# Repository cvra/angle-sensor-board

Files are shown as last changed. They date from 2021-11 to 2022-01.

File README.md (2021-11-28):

# Carte Codeur Absolu

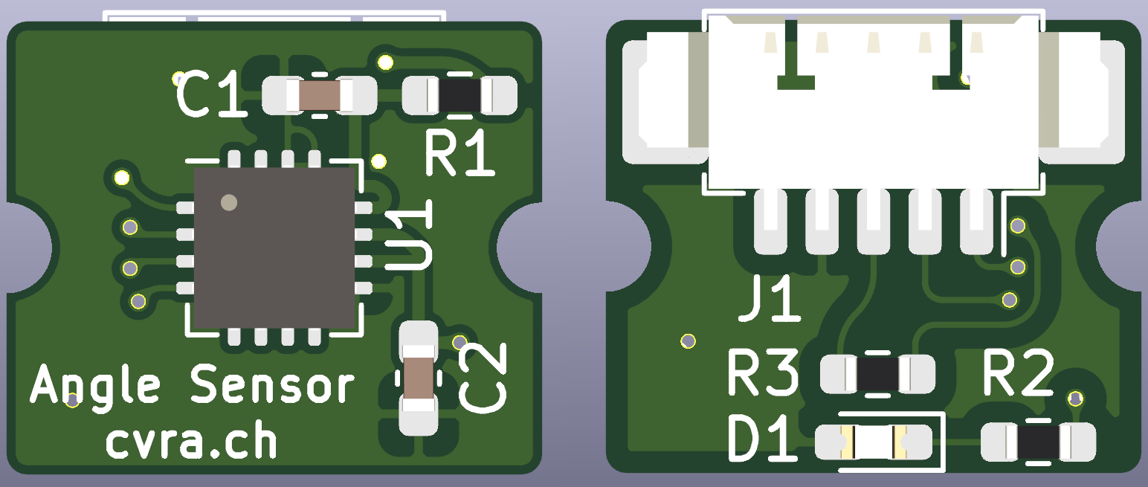
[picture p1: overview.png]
3D rendering of the board


## Cahier des charges

### Général

* Le but de cette carte est de fournir une information de position angulaire absolue, c'est-à-dire un angle par rapport à une position de référence.
* La carte se connecte à une carte moteur CVRA pour en augmenter les capacités.
* La carte fournit 4096 points par tour.
* La carte est assemblable à la main, mais peut nécessiter un pochoir pour les composants SMD.

### Electronique

* Alimentation: 20mA @ 3.3V.
* Connection compatible avec le connecteur de la carte moteur (P3 sur [ce schéma](https://github.com/cvra/motor-control-board/raw/revA/Moteur.pdf).
* Interface SPI.
* Branchement par un connecteur PicoBlade 5 pin.
* LED pour indiquer l’alimentation.
* Respecte les [design rules Aisler](https://aisler.net/help/design-rules-and-specifications/design-rules).
* Taille des passifs: 0603.

## Mécanique

* le plus petit possible (13mmx11mm)
* 2x demi trous M2 sur bord opposée
* connecteur sortie parallèle au PCB, sur face opposée au capteur
* LED sur la même face que le connecteur
* Capteur centré au milieux des vis

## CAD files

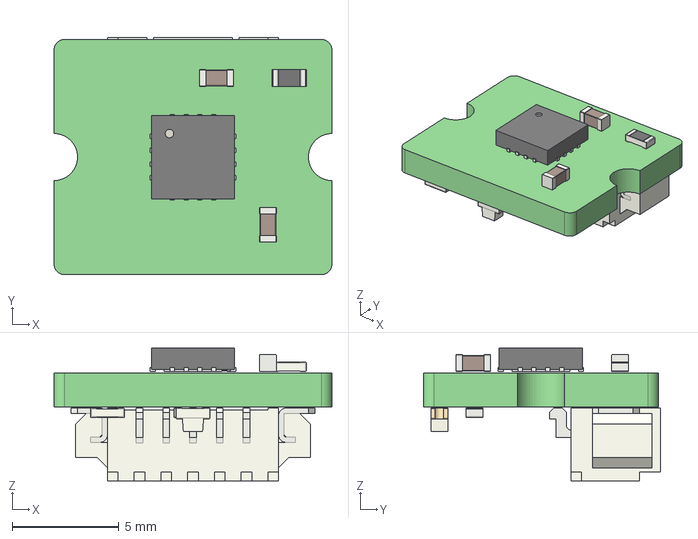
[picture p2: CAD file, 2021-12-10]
angle-sensor-board.step
13.0 x 11.1 x 6.20 mm

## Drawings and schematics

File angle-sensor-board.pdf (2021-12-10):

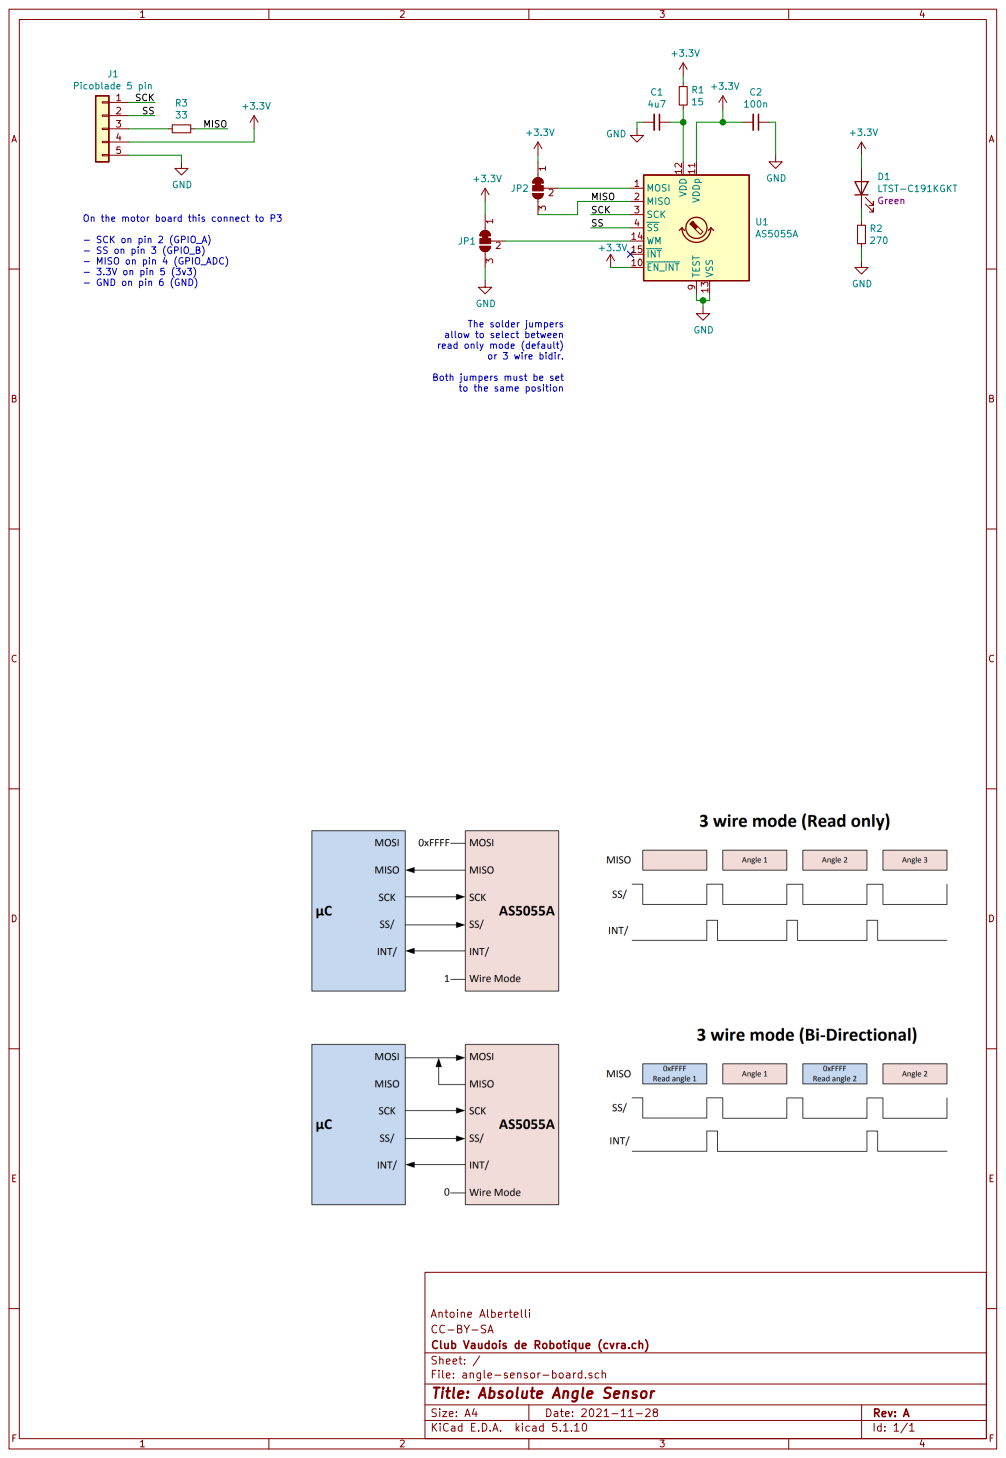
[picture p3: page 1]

SS On the motor board this connect to P3

- SCK on pin 2 (GPIO_A)
- SS on pin 3 (GPIO_B)
- MISO on pin 4 (GPIO_ADC)
- 3.3V on pin 5 (3v3)
- GND on pin 6 (GND)

The solder jumpers allow to select between

read only mode (default) or 3 wire bidir. Both jumpers must be set

to the same position

Antoine Albertelli
File: angle-sensor-board.sch Sheet: / Club Vaudois de Robotique (cvra.ch) CC-BY-SA

Id: 1/1 Title: Absolute Angle Sensor

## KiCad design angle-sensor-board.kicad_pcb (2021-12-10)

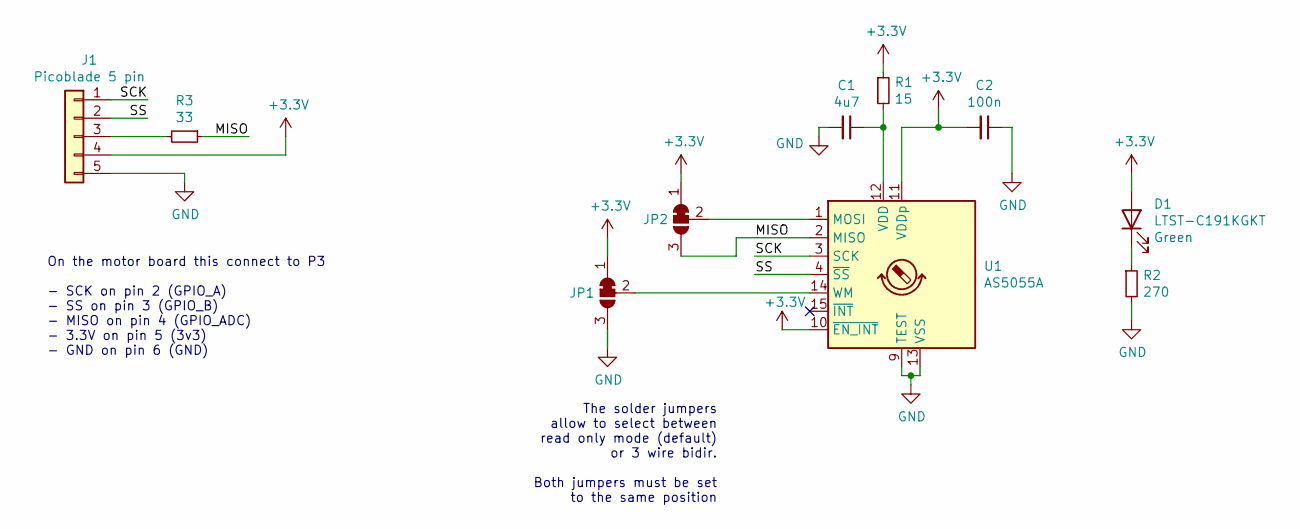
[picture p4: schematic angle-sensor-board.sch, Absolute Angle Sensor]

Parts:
C1: 4u7; C_0603_1608Metric_Pad1.08x0.95mm_HandSolder; digikey# 1276-1045-1-ND
C2: 100n; C_0603_1608Metric_Pad1.08x0.95mm_HandSolder; digikey# 1276-1006-1-ND
D1: LTST-C191KGKT; LED_0603_1608Metric_Castellated; digikey# 160-1446-1-ND
J1: Picoblade 5 pin; Molex_PicoBlade_53261-0571_1x05-1MP_P1.25mm_Horizontal; digikey# WM7623CT-ND
JP1, JP2: SolderJumper_3_Bridged12; SolderJumper-3_P1.3mm_Bridged12_RoundedPad1.0x1.5mm
R1: 15; R_0603_1608Metric_Pad0.98x0.95mm_HandSolder; digikey# A129666CT-ND
R2: 270; R_0603_1608Metric_Pad0.98x0.95mm_HandSolder; digikey# A129681CT-ND
R3: 33; R_0603_1608Metric_Pad0.98x0.95mm_HandSolder; digikey# A130082CT-ND
U1: AS5055A; QFN-16-1EP_4x4mm_P0.65mm_EP2.7x2.7mm; digikey# AS5055A-BQFMCT-ND

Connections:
+3V3: C2.2, D1.2 (A), J1.4, JP1.1 (A), JP2.1 (A), R1.1, U1.10 (~EN_INT), U1.11 (VDDp)
/MISO: JP2.3 (B), R3.1, U1.2 (MISO)
/SCK: J1.1, U1.3 (SCK)
/SS: J1.2, U1.4 (~SS)
GND: C1.2, C2.1, J1.5, JP1.3 (B), R2.2, U1.9 (TEST), U1.13 (VSS)
unnamed: C1.1, R1.2, U1.12 (VDD)
unnamed: D1.1 (K), R2.1
unnamed: J1.3, R3.2
unnamed: JP1.2 (C), U1.14 (WM)
unnamed: JP2.2 (C), U1.1 (MOSI)

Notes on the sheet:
On the motor board this connect to P3 - SCK on pin 2 (GPIO_A) - SS on pin 3 (GPIO_B) - MISO on pin 4 (GPIO_ADC) - 3.3V on pin 5 (3v3) - GND on pin 6 (GND)
The solder jumpers allow to select between read only mode (default) or 3 wire bidir. Both jumpers must be set to the same position

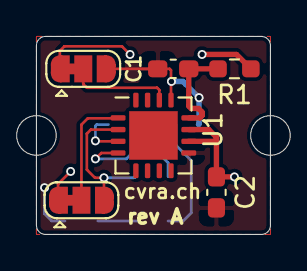
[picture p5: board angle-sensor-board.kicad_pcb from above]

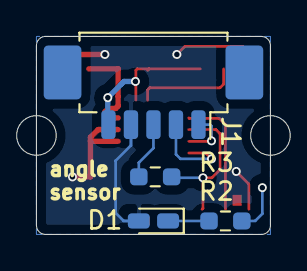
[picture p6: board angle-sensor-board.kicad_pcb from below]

Board: 2 copper layers, 13.0 x 11.0 mm, 10 parts (4 on the bottom side), 10 nets.

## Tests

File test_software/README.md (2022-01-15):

# ESP32 firmware to test the board

`ams.py` contains [MicroPython](https://docs.micropython.org/en/latest/esp32/quickref.html) code to test the angle sensor.
It will read the sensor's output and print in in the terminal.
To run it, after installing MicroPython on the ESP32, run the following command on your computer:

```shell
./pyboard.py ams.py --device /dev/tty.SLAB_USBtoUART
```

You can interrupt it by pressing Ctrl-C.

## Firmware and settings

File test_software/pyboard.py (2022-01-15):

#!/usr/bin/env python3
#
# This file is part of the MicroPython project, http://micropython.org/
#
# The MIT License (MIT)
#
# Copyright (c) 2014-2021 Damien P. George
# Copyright (c) 2017 Paul Sokolovsky
#
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
"""
pyboard interface

This module provides the Pyboard class, used to communicate with and
control a MicroPython device over a communication channel. Both real
boards and emulated devices (e.g. running in QEMU) are supported.
Various communication channels are supported, including a serial
connection, telnet-style network connection, external process
connection.

Example usage:

    import pyboard
    pyb = pyboard.Pyboard('/dev/ttyACM0')

Or:

    pyb = pyboard.Pyboard('192.168.1.1')

Then:

    pyb.enter_raw_repl()
    pyb.exec('import pyb')
    pyb.exec('pyb.LED(1).on()')
    pyb.exit_raw_repl()

Note: if using Python2 then pyb.exec must be written as pyb.exec_.
To run a script from the local machine on the board and print out the results:

    import pyboard
    pyboard.execfile('test.py', device='/dev/ttyACM0')

This script can also be run directly.  To execute a local script, use:

    ./pyboard.py test.py

Or:

    python pyboard.py test.py

"""

import sys
import time
import os
import ast

try:
    stdout = sys.stdout.buffer
except AttributeError:
    # Python2 doesn't have buffer attr
    stdout = sys.stdout


def stdout_write_bytes(b):
    b = b.replace(b"\x04", b"")
    stdout.write(b)
    stdout.flush()


class PyboardError(Exception):
    pass


class TelnetToSerial:
    def __init__(self, ip, user, password, read_timeout=None):
        self.tn = None
        import telnetlib

        self.tn = telnetlib.Telnet(ip, timeout=15)
        self.read_timeout = read_timeout
        if b"Login as:" in self.tn.read_until(b"Login as:", timeout=read_timeout):
            self.tn.write(bytes(user, "ascii") + b"\r\n")

            if b"Password:" in self.tn.read_until(b"Password:", timeout=read_timeout):
                # needed because of internal implementation details of the telnet server
                time.sleep(0.2)
                self.tn.write(bytes(password, "ascii") + b"\r\n")

                if b"for more information." in self.tn.read_until(
                    b'Type "help()" for more information.', timeout=read_timeout
                ):
                    # login successful
                    from collections import deque

                    self.fifo = deque()
                    return

        raise PyboardError("Failed to establish a telnet connection with the board")

    def __del__(self):
        self.close()

    def close(self):
        if self.tn:
            self.tn.close()

    def read(self, size=1):
        while len(self.fifo) < size:
            timeout_count = 0
            data = self.tn.read_eager()
            if len(data):
                self.fifo.extend(data)
                timeout_count = 0
            else:
                time.sleep(0.25)
                if self.read_timeout is not None and timeout_count > 4 * self.read_timeout:
                    break
                timeout_count += 1

        data = b""
        while len(data) < size and len(self.fifo) > 0:
            data += bytes([self.fifo.popleft()])
        return data

    def write(self, data):
        self.tn.write(data)
        return len(data)

    def inWaiting(self):
        n_waiting = len(self.fifo)
        if not n_waiting:
            data = self.tn.read_eager()
            self.fifo.extend(data)
            return len(data)
        else:
            return n_waiting


class ProcessToSerial:
    "Execute a process and emulate serial connection using its stdin/stdout."

    def __init__(self, cmd):
        import subprocess

        self.subp = subprocess.Popen(
            cmd,
            bufsize=0,
            shell=True,
            preexec_fn=os.setsid,
            stdin=subprocess.PIPE,
            stdout=subprocess.PIPE,
        )

        # Initially was implemented with selectors, but that adds Python3
        # dependency. However, there can be race conditions communicating
        # with a particular child process (like QEMU), and selectors may
        # still work better in that case, so left inplace for now.
        #
        # import selectors
        # self.sel = selectors.DefaultSelector()
        # self.sel.register(self.subp.stdout, selectors.EVENT_READ)

        import select

        self.poll = select.poll()
        self.poll.register(self.subp.stdout.fileno())

    def close(self):
        import signal

        os.killpg(os.getpgid(self.subp.pid), signal.SIGTERM)

    def read(self, size=1):
        data = b""
        while len(data) < size:
            data += self.subp.stdout.read(size - len(data))
        return data

    def write(self, data):
        self.subp.stdin.write(data)
        return len(data)

    def inWaiting(self):
        # res = self.sel.select(0)
        res = self.poll.poll(0)
        if res:
            return 1
        return 0


class ProcessPtyToTerminal:
    """Execute a process which creates a PTY and prints slave PTY as
    first line of its output, and emulate serial connection using
    this PTY."""

    def __init__(self, cmd):
        import subprocess
        import re
        import serial

        self.subp = subprocess.Popen(
            cmd.split(),
            bufsize=0,
            shell=False,
            preexec_fn=os.setsid,
            stdin=subprocess.PIPE,
            stdout=subprocess.PIPE,
            stderr=subprocess.PIPE,
        )
        pty_line = self.subp.stderr.readline().decode("utf-8")
        m = re.search(r"/dev/pts/[0-9]+", pty_line)
        if not m:
            print("Error: unable to find PTY device in startup line:", pty_line)
            self.close()
            sys.exit(1)
        pty = m.group()
        # rtscts, dsrdtr params are to workaround pyserial bug:
        # http://stackoverflow.com/questions/34831131/pyserial-does-not-play-well-with-virtual-port
        self.ser = serial.Serial(pty, interCharTimeout=1, rtscts=True, dsrdtr=True)

    def close(self):
        import signal

        os.killpg(os.getpgid(self.subp.pid), signal.SIGTERM)

    def read(self, size=1):
        return self.ser.read(size)

    def write(self, data):
        return self.ser.write(data)

    def inWaiting(self):
        return self.ser.inWaiting()


class Pyboard:
    def __init__(
        self, device, baudrate=115200, user="micro", password="python", wait=0, exclusive=True
    ):
        self.in_raw_repl = False
        self.use_raw_paste = True
        if device.startswith("exec:"):
            self.serial = ProcessToSerial(device[len("exec:") :])
        elif device.startswith("execpty:"):
            self.serial = ProcessPtyToTerminal(device[len("qemupty:") :])
        elif device and device[0].isdigit() and device[-1].isdigit() and device.count(".") == 3:
            # device looks like an IP address
            self.serial = TelnetToSerial(device, user, password, read_timeout=10)
        else:
            import serial

            # Set options, and exclusive if pyserial supports it
            serial_kwargs = {"baudrate": baudrate, "interCharTimeout": 1}
            if serial.__version__ >= "3.3":
                serial_kwargs["exclusive"] = exclusive

            delayed = False
            for attempt in range(wait + 1):
                try:
                    self.serial = serial.Serial(device, **serial_kwargs)
                    break
                except (OSError, IOError):  # Py2 and Py3 have different errors
                    if wait == 0:
                        continue
                    if attempt == 0:
                        sys.stdout.write("Waiting {} seconds for pyboard ".format(wait))
                        delayed = True
                time.sleep(1)
                sys.stdout.write(".")
                sys.stdout.flush()
            else:
                if delayed:
                    print("")
                raise PyboardError("failed to access " + device)
            if delayed:
                print("")

    def close(self):
        self.serial.close()

    def read_until(self, min_num_bytes, ending, timeout=10, data_consumer=None):
        # if data_consumer is used then data is not accumulated and the ending must be 1 byte long
        assert data_consumer is None or len(ending) == 1

        data = self.serial.read(min_num_bytes)
        if data_consumer:
            data_consumer(data)
        timeout_count = 0
        while True:
            if data.endswith(ending):
                break
            elif self.serial.inWaiting() > 0:
                new_data = self.serial.read(1)
                if data_consumer:
                    data_consumer(new_data)
                    data = new_data
                else:
                    data = data + new_data
                timeout_count = 0
            else:
                timeout_count += 1
                if timeout is not None and timeout_count >= 100 * timeout:
                    break
                time.sleep(0.01)
        return data

    def enter_raw_repl(self, soft_reset=True):
        self.serial.write(b"\r\x03\x03")  # ctrl-C twice: interrupt any running program

        # flush input (without relying on serial.flushInput())
        n = self.serial.inWaiting()
        while n > 0:
            self.serial.read(n)
            n = self.serial.inWaiting()

        self.serial.write(b"\r\x01")  # ctrl-A: enter raw REPL

        if soft_reset:
            data = self.read_until(1, b"raw REPL; CTRL-B to exit\r\n>")
            if not data.endswith(b"raw REPL; CTRL-B to exit\r\n>"):
                print(data)
                raise PyboardError("could not enter raw repl")

            self.serial.write(b"\x04")  # ctrl-D: soft reset

            # Waiting for "soft reboot" independently to "raw REPL" (done below)
            # allows boot.py to print, which will show up after "soft reboot"
            # and before "raw REPL".
            data = self.read_until(1, b"soft reboot\r\n")
            if not data.endswith(b"soft reboot\r\n"):
                print(data)
                raise PyboardError("could not enter raw repl")

        data = self.read_until(1, b"raw REPL; CTRL-B to exit\r\n")
        if not data.endswith(b"raw REPL; CTRL-B to exit\r\n"):
            print(data)
            raise PyboardError("could not enter raw repl")

        self.in_raw_repl = True

    def exit_raw_repl(self):
        self.serial.write(b"\r\x02")  # ctrl-B: enter friendly REPL
        self.in_raw_repl = False

    def follow(self, timeout, data_consumer=None):
        # wait for normal output
        data = self.read_until(1, b"\x04", timeout=timeout, data_consumer=data_consumer)
        if not data.endswith(b"\x04"):
            raise PyboardError("timeout waiting for first EOF reception")
        data = data[:-1]

        # wait for error output
        data_err = self.read_until(1, b"\x04", timeout=timeout)
        if not data_err.endswith(b"\x04"):
            raise PyboardError("timeout waiting for second EOF reception")
        data_err = data_err[:-1]

        # return normal and error output
        return data, data_err

    def raw_paste_write(self, command_bytes):
        # Read initial header, with window size.
        data = self.serial.read(2)
        window_size = data[0] | data[1] << 8
        window_remain = window_size

        # Write out the command_bytes data.
        i = 0
        while i < len(command_bytes):
            while window_remain == 0 or self.serial.inWaiting():
                data = self.serial.read(1)
                if data == b"\x01":
                    # Device indicated that a new window of data can be sent.
                    window_remain += window_size
                elif data == b"\x04":
                    # Device indicated abrupt end.  Acknowledge it and finish.
                    self.serial.write(b"\x04")
                    return
                else:
                    # Unexpected data from device.
                    raise PyboardError("unexpected read during raw paste: {}".format(data))
            # Send out as much data as possible that fits within the allowed window.
            b = command_bytes[i : min(i + window_remain, len(command_bytes))]
            self.serial.write(b)
            window_remain -= len(b)
            i += len(b)

        # Indicate end of data.
        self.serial.write(b"\x04")

        # Wait for device to acknowledge end of data.
        data = self.read_until(1, b"\x04")
        if not data.endswith(b"\x04"):
            raise PyboardError("could not complete raw paste: {}".format(data))

    def exec_raw_no_follow(self, command):
        if isinstance(command, bytes):
            command_bytes = command
        else:
            command_bytes = bytes(command, encoding="utf8")

        # check we have a prompt
        data = self.read_until(1, b">")
        if not data.endswith(b">"):
            raise PyboardError("could not enter raw repl")

        if self.use_raw_paste:
            # Try to enter raw-paste mode.
            self.serial.write(b"\x05A\x01")
            data = self.serial.read(2)
            if data == b"R\x00":
                # Device understood raw-paste command but doesn't support it.
                pass
            elif data == b"R\x01":
                # Device supports raw-paste mode, write out the command using this mode.
                return self.raw_paste_write(command_bytes)
            else:
                # Device doesn't support raw-paste, fall back to normal raw REPL.
                data = self.read_until(1, b"w REPL; CTRL-B to exit\r\n>")
                if not data.endswith(b"w REPL; CTRL-B to exit\r\n>"):
                    print(data)
                    raise PyboardError("could not enter raw repl")
            # Don't try to use raw-paste mode again for this connection.
            self.use_raw_paste = False

        # Write command using standard raw REPL, 256 bytes every 10ms.
        for i in range(0, len(command_bytes), 256):
            self.serial.write(command_bytes[i : min(i + 256, len(command_bytes))])
            time.sleep(0.01)
        self.serial.write(b"\x04")

        # check if we could exec command
        data = self.serial.read(2)
        if data != b"OK":
            raise PyboardError("could not exec command (response: %r)" % data)

    def exec_raw(self, command, timeout=10, data_consumer=None):
        self.exec_raw_no_follow(command)
        return self.follow(timeout, data_consumer)

    def eval(self, expression):
        ret = self.exec_("print({})".format(expression))
        ret = ret.strip()
        return ret

    def exec_(self, command, data_consumer=None):
        ret, ret_err = self.exec_raw(command, data_consumer=data_consumer)
        if ret_err:
            raise PyboardError("exception", ret, ret_err)
        return ret

    def execfile(self, filename):
        with open(filename, "rb") as f:
            pyfile = f.read()
        return self.exec_(pyfile)

    def get_time(self):
        t = str(self.eval("pyb.RTC().datetime()"), encoding="utf8")[1:-1].split(", ")
        return int(t[4]) * 3600 + int(t[5]) * 60 + int(t[6])

    def fs_ls(self, src):
        cmd = (
            "import uos\nfor f in uos.ilistdir(%s):\n"
            " print('{:12} {}{}'.format(f[3]if len(f)>3 else 0,f[0],'/'if f[1]&0x4000 else ''))"
            % (("'%s'" % src) if src else "")
        )
        self.exec_(cmd, data_consumer=stdout_write_bytes)

    def fs_cat(self, src, chunk_size=256):
        cmd = (
            "with open('%s') as f:\n while 1:\n"
            "  b=f.read(%u)\n  if not b:break\n  print(b,end='')" % (src, chunk_size)
        )
        self.exec_(cmd, data_consumer=stdout_write_bytes)

    def fs_get(self, src, dest, chunk_size=256):
        self.exec_("f=open('%s','rb')\nr=f.read" % src)
        with open(dest, "wb") as f:
            while True:
                data = bytearray()
                self.exec_("print(r(%u))" % chunk_size, data_consumer=lambda d: data.extend(d))
                assert data.endswith(b"\r\n\x04")
                try:
                    data = ast.literal_eval(str(data[:-3], "ascii"))
                    if not isinstance(data, bytes):
                        raise ValueError("Not bytes")
                except (UnicodeError, ValueError) as e:
                    raise PyboardError("fs_get: Could not interpret received data: %s" % str(e))
                if not data:
                    break
                f.write(data)
        self.exec_("f.close()")

    def fs_put(self, src, dest, chunk_size=256):
        self.exec_("f=open('%s','wb')\nw=f.write" % dest)
        with open(src, "rb") as f:
            while True:
                data = f.read(chunk_size)
                if not data:
                    break
                if sys.version_info < (3,):
                    self.exec_("w(b" + repr(data) + ")")
                else:
                    self.exec_("w(" + repr(data) + ")")
        self.exec_("f.close()")

    def fs_mkdir(self, dir):
        self.exec_("import uos\nuos.mkdir('%s')" % dir)

    def fs_rmdir(self, dir):
        self.exec_("import uos\nuos.rmdir('%s')" % dir)

    def fs_rm(self, src):
        self.exec_("import uos\nuos.remove('%s')" % src)


# in Python2 exec is a keyword so one must use "exec_"
# but for Python3 we want to provide the nicer version "exec"
setattr(Pyboard, "exec", Pyboard.exec_)


def execfile(filename, device="/dev/ttyACM0", baudrate=115200, user="micro", password="python"):
    pyb = Pyboard(device, baudrate, user, password)
    pyb.enter_raw_repl()
    output = pyb.execfile(filename)
    stdout_write_bytes(output)
    pyb.exit_raw_repl()
    pyb.close()


def filesystem_command(pyb, args):
    def fname_remote(src):
        if src.startswith(":"):
            src = src[1:]
        return src

    def fname_cp_dest(src, dest):
        src = src.rsplit("/", 1)[-1]
        if dest is None or dest == "":
            dest = src
        elif dest == ".":
            dest = "./" + src
        elif dest.endswith("/"):
            dest += src
        return dest

    cmd = args[0]
    args = args[1:]
    try:
        if cmd == "cp":
            srcs = args[:-1]
            dest = args[-1]
            if srcs[0].startswith("./") or dest.startswith(":"):
                op = pyb.fs_put
                fmt = "cp %s :%s"
                dest = fname_remote(dest)
            else:
                op = pyb.fs_get
                fmt = "cp :%s %s"
            for src in srcs:
                src = fname_remote(src)
                dest2 = fname_cp_dest(src, dest)
                print(fmt % (src, dest2))
                op(src, dest2)
        else:
            op = {
                "ls": pyb.fs_ls,
                "cat": pyb.fs_cat,
                "mkdir": pyb.fs_mkdir,
                "rmdir": pyb.fs_rmdir,
                "rm": pyb.fs_rm,
            }[cmd]
            if cmd == "ls" and not args:
                args = [""]
            for src in args:
                src = fname_remote(src)
                print("%s :%s" % (cmd, src))
                op(src)
    except PyboardError as er:
        print(str(er.args[2], "ascii"))
        pyb.exit_raw_repl()
        pyb.close()
        sys.exit(1)


_injected_import_hook_code = """\
import uos, uio
class _FS:
  class File(uio.IOBase):
    def __init__(self):
      self.off = 0
    def ioctl(self, request, arg):
      return 0
    def readinto(self, buf):
      buf[:] = memoryview(_injected_buf)[self.off:self.off + len(buf)]
      self.off += len(buf)
      return len(buf)
  mount = umount = chdir = lambda *args: None
  def stat(self, path):
    if path == '_injected.mpy':
      return tuple(0 for _ in range(10))
    else:
      raise OSError(-2) # ENOENT
  def open(self, path, mode):
    return self.File()
uos.mount(_FS(), '/_')
uos.chdir('/_')
from _injected import *
uos.umount('/_')
del _injected_buf, _FS
"""
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

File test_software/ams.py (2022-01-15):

from time import sleep
from machine import Pin, SPI
import struct

PRINT_RAW = False

sck_pin = Pin(19, value=0)  # Brown wire, connector pin 1
ss_pin = Pin(21, Pin.OUT, value=1)  # Red wire, connector pin 2
miso_pin = Pin(18)  # Orange wire, connector pin 3
mosi_pin = Pin(5)  # Unconected

spi = SPI(
    1,
    baudrate=1_000_000,
    polarity=0,
    phase=1,
    sck=sck_pin,
    mosi=mosi_pin,
    miso=miso_pin,
)


def read_sensor():
    # Read 2 bytes from the sensor
    ss_pin.value(0)
    data = spi.read(2)
    ss_pin.value(1)

    # Convert the 2 bytes to a 16-bit number
    decoded = struct.unpack("!H", data)[0]

    # Discard the first two bits, which are used for parity errors
    decoded = decoded >> 2

    # Extract the alarm bits for magnetic field too high or too low
    alarm = (decoded & (0b11 << 12)) >> 12
    if alarm & 1:
        high = "H"
    else:
        high = " "
    if alarm & 2:
        low = "L"
    else:
        low = " "

    # Keep the 12 bits of data
    decoded = decoded & 0xFFF

    # Sometimes, the decoded signal is zero, why ?
    if decoded == 0:
        return

    if PRINT_RAW:
        print("{}{} {:05d}".format(high, low, decoded))
    else:
        angle = int(360.0 * decoded / 4096.0)
        print("{:03d}".format(angle))


while True:
    read_sensor()
    sleep(0.01)

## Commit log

2021-11-28 Initial design
    [angle-sensor-board.kicad_pcb, angle-sensor-board.sch]
2021-12-02 Add digikey references for passives
    [angle-sensor-board.sch]
2021-12-10 Add some solder jumpers to select modes
    [angle-sensor-board.kicad_pcb]
2021-12-10 Add production output files
    [angle-sensor-board-B_Cu.gbl, angle-sensor-board-B_Mask.gbs, angle-sensor-board-B_Paste.gbp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]
2021-12-10 Add missing prod files
    [angle-sensor-board-NPTH.drl, angle-sensor-board-PTH.drl]
2022-01-15 Add some test software to check if the PCBs are working
